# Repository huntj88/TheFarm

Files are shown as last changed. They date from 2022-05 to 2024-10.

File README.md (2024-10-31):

# TheFarm
High Pressure Aeroponics Experiment - <a href="https://photos.app.goo.gl/xgiAT7T5yuNJSb9R8">Project photo/video album</a>

Lettuce
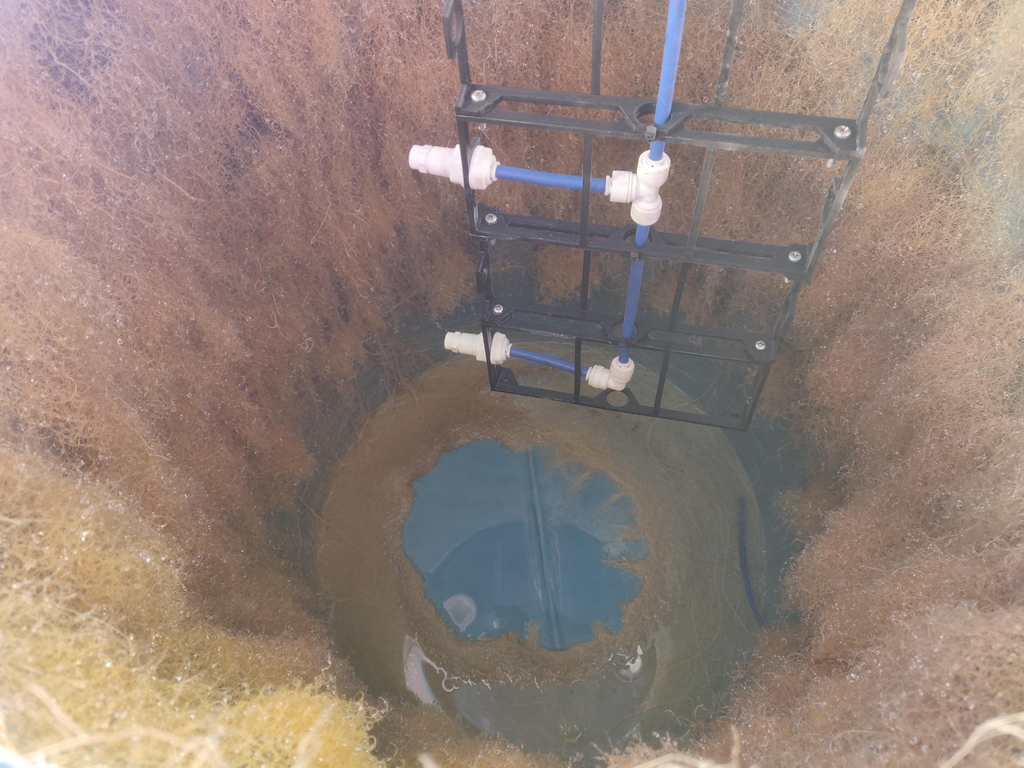
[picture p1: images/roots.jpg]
Lettuce


## Features
* High pressure dispersion system
  * Maximized water usage, minimized waste that is drained off
  * Rotary Dispersion system
    * Equal dispersion
    * High plant/nozzle ratio
    * Very few nozzles to maintain pressure through the system
      * This could be achieved by different watering zones that turn on sequentially to maintain pressure, but some water is wasted at the start/end when pressure is not enough for aerosolization to occur.
* Automatic LED Lighting Configurable by software.
* Environmental Monitoring / Correction
  * Temperature and Humidity Monitoring
  * Automatic humidity correction
    * humidifier enabled based on vapor pressure deficit
    * Doing this in a grow tent was crucial for maintaining correct humidity
  * No Temperature Control, at the mercy of my decently insulated garage.
* Time Lapse Camera
  * Old Android device with an app that took a picture and uploaded it to S3. App was triggered periodically over ADB from a raspberry pi.
* Water reservoir level monitoring
  * Sonic sensor was used to find depth of the water tank, which was converted into a percent of remaining water.
* The Software integrated all of the above together
  * Based on events, the whole system is reactive to new data.
  * Historical events are Recorded in InfluxDB time series database.
  * Devices are controlled in a variety of manners
    * Wifi using mqtt
    * USB (android camera only)
    * Smart power strips with local network api.
      * Turning on on the High Pressure pump periodically.
      * Controlling lights on/off cycles
  * Energy Monitoring with smart power strips.

## Reliability
High reliability was a priority. This is the only project I've had where I was really forced to wait around on the time scale that plants grow at. This is magnified by the use of aeroponics which allows the roots to dry out very quickly if something goes wrong. Starting over is no fun.

There was at least two times where I left home for awhile, only to come back to my plants being dead. There were several other occasions where my plants were effecively on manual life support while I debugged issues.

I spent a lot of time ensuring my plants wouldn't die on me, and that everything would come back online automatically after events like a power outage, network issues, process failures, etc.

For my most recent crop, I let it do it's thing for weeks at a time without any intervention except to refill consumables.

## Barrel Changes

### V1
Initially I used pvc to make net cup mounts because it was readily available. Unfortunately cuttings ovals into the barrel was pretty time consuming. I also should've cut the pvc closer to the barrel, as it prevented water from getting to the base of the roots.

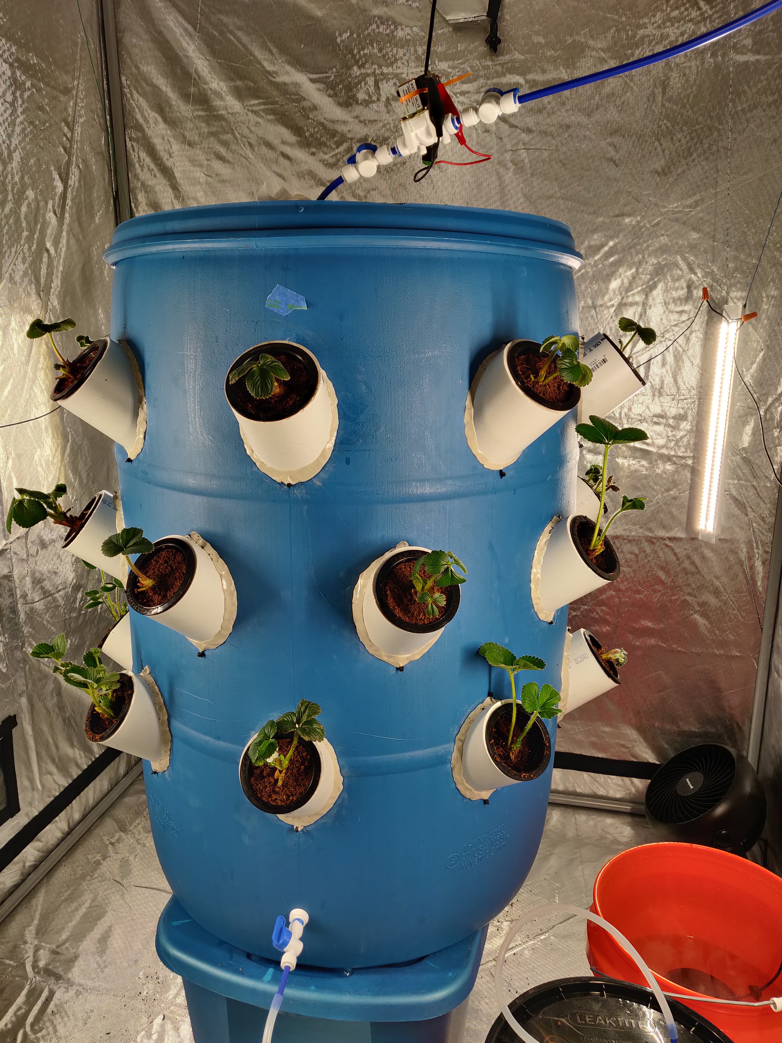
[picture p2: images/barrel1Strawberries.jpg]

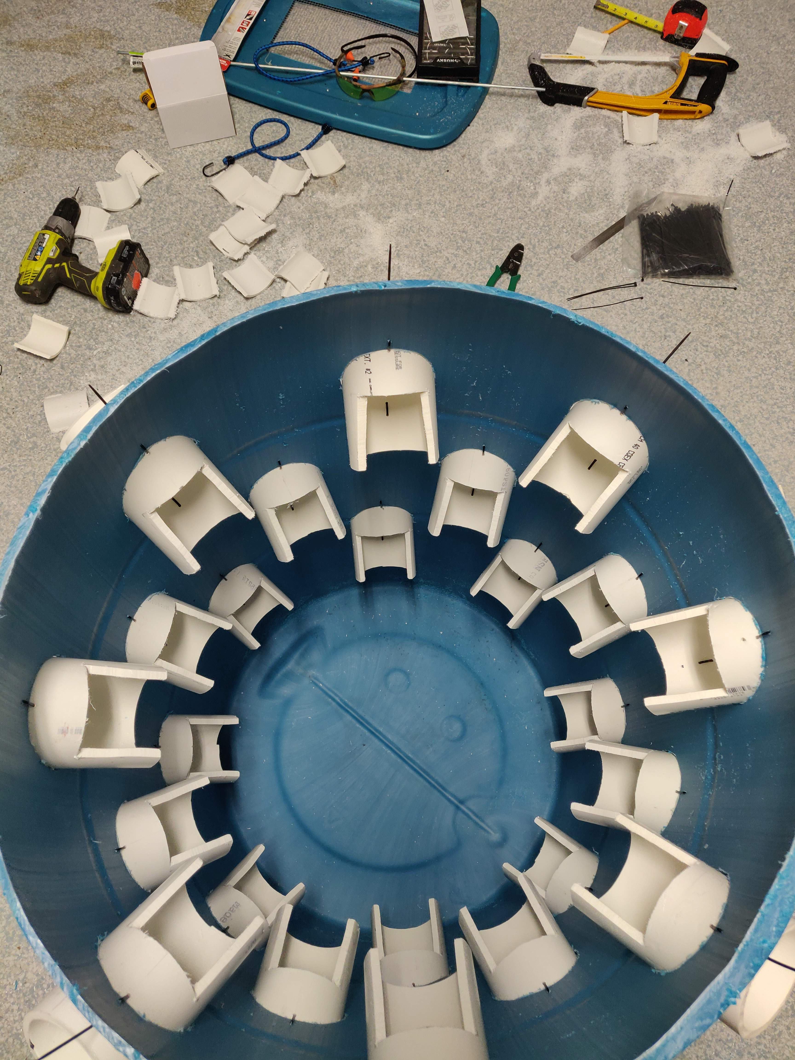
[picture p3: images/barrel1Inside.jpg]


This setup did work for strawberries until I killed my plants from a software issue, but I started with dormant bare root strawberry plants that had roots long enough to not cause issues.

I tried on lettuce and this setup did not work at all.

---

### V2
For V2 of the barrel I wanted to cut down on manual labor for myself, so I designed this net cup bracket and 3D printed 48 of them. I used a 3 inch hole saw to cut the holes, and secured the brackets in place with stainless steel machine screws.

The curvature is TINY bit too aggressive, so I would fix that If I printed a new batch.

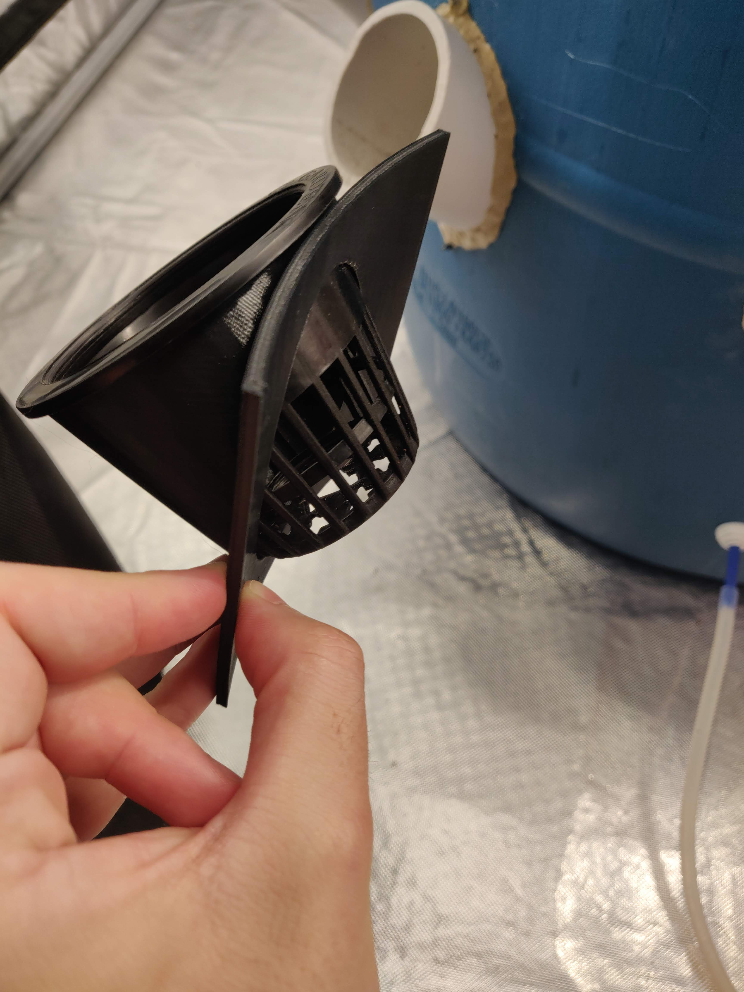
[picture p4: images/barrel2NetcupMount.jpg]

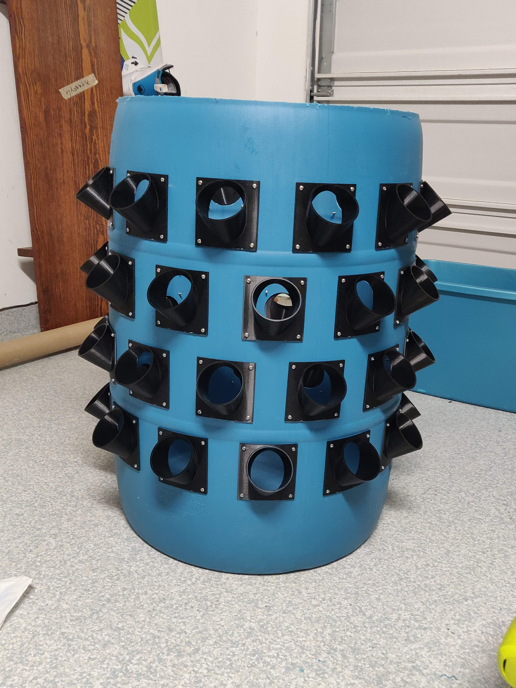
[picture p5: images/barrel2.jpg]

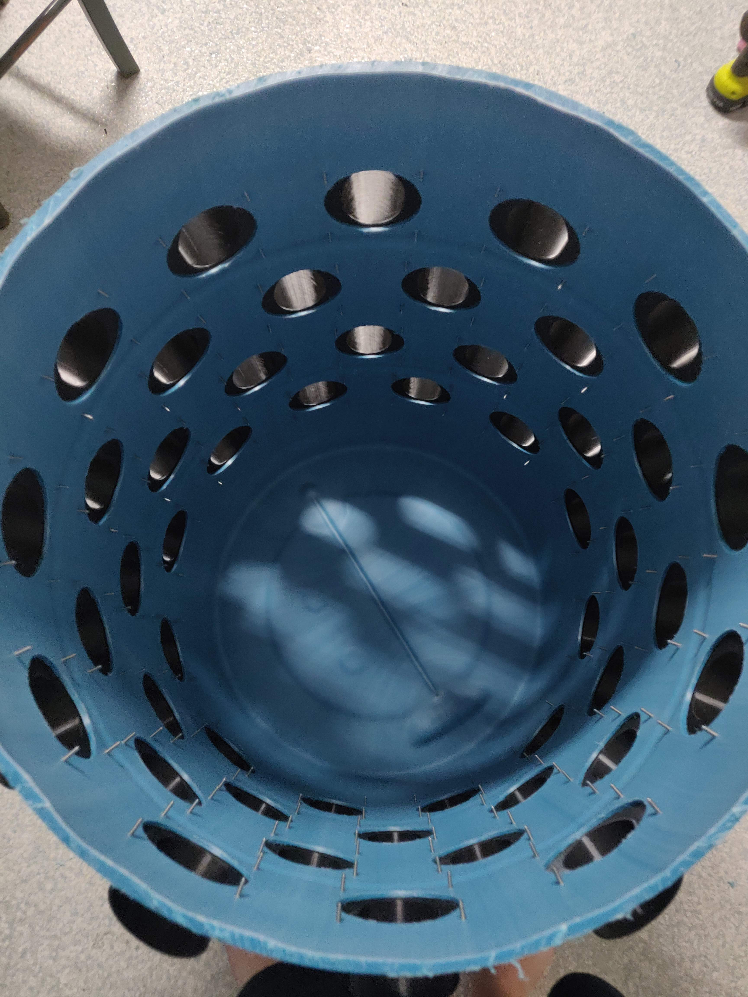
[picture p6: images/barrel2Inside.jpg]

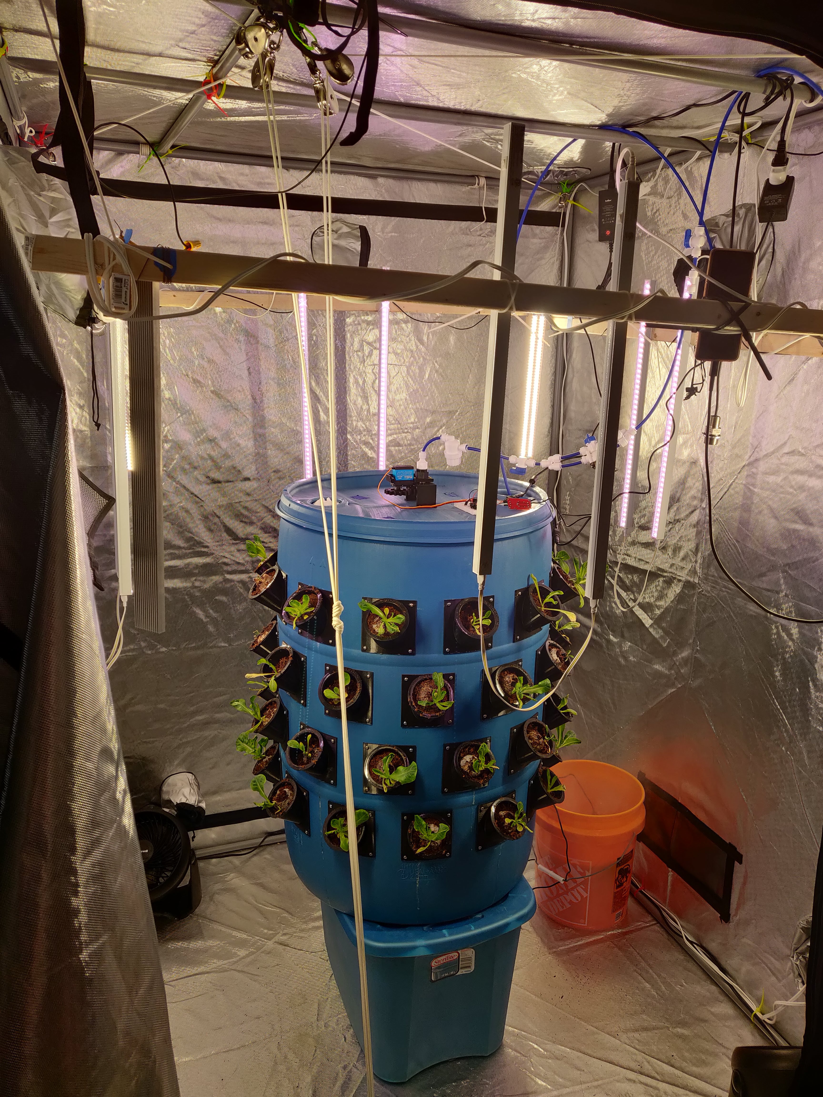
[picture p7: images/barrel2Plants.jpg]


## Mister changes
I started out with Knex just to understand the spray pattern my misters had

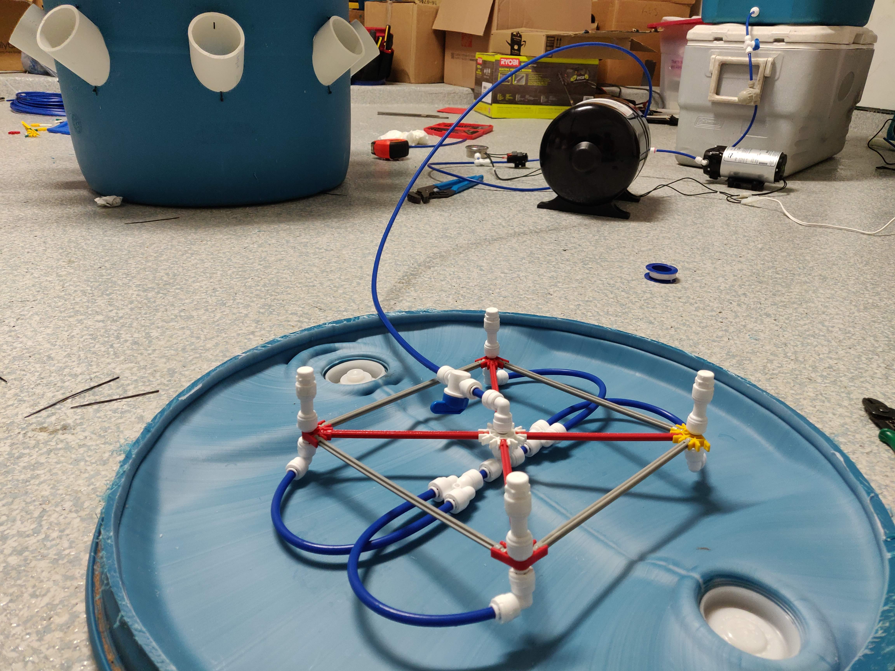
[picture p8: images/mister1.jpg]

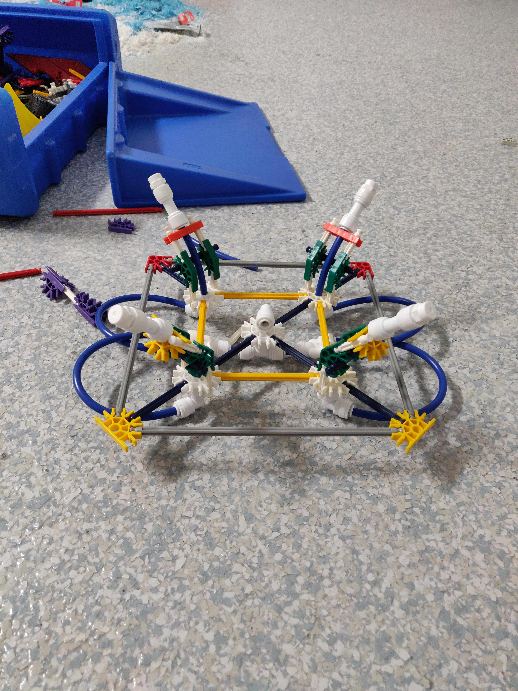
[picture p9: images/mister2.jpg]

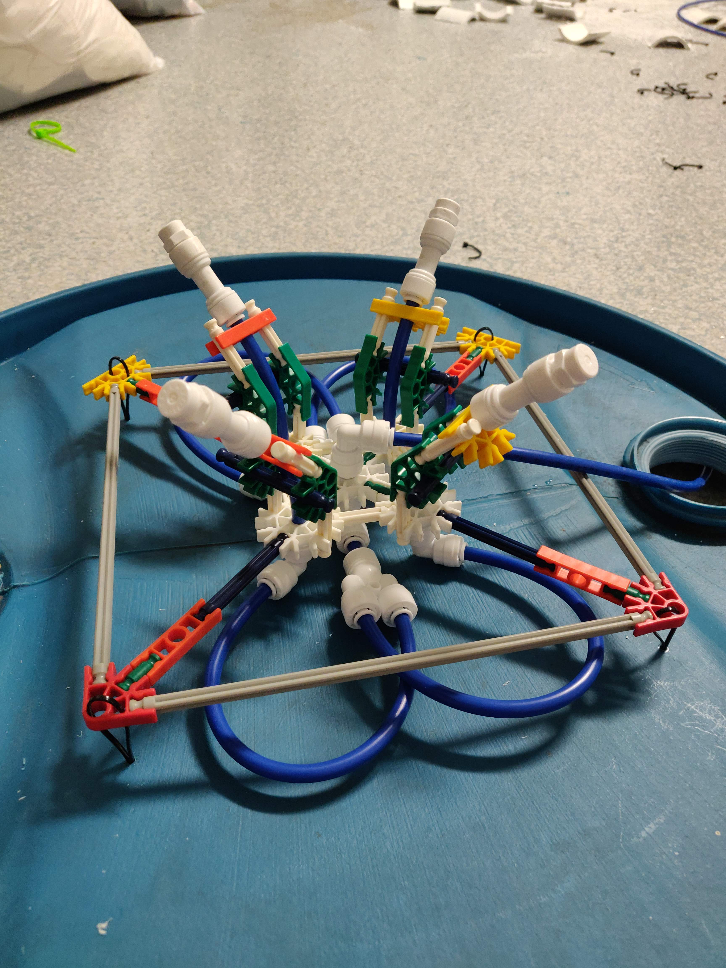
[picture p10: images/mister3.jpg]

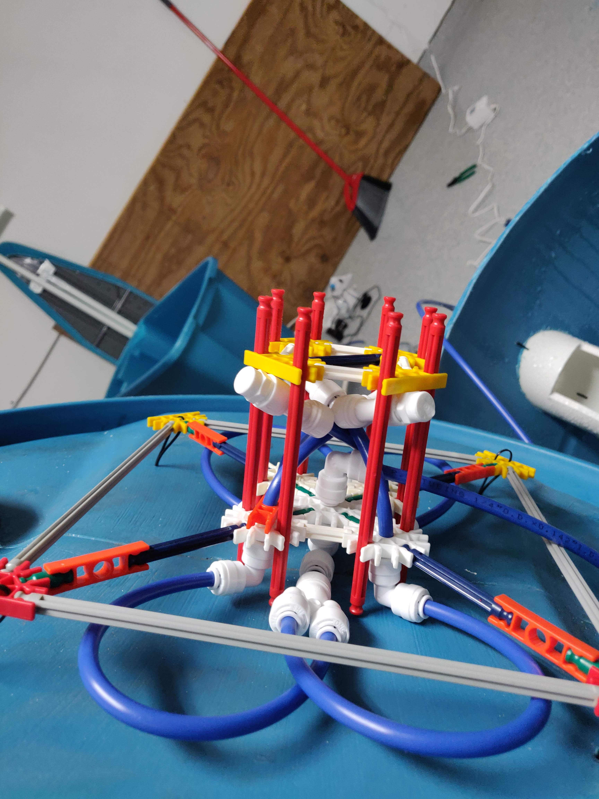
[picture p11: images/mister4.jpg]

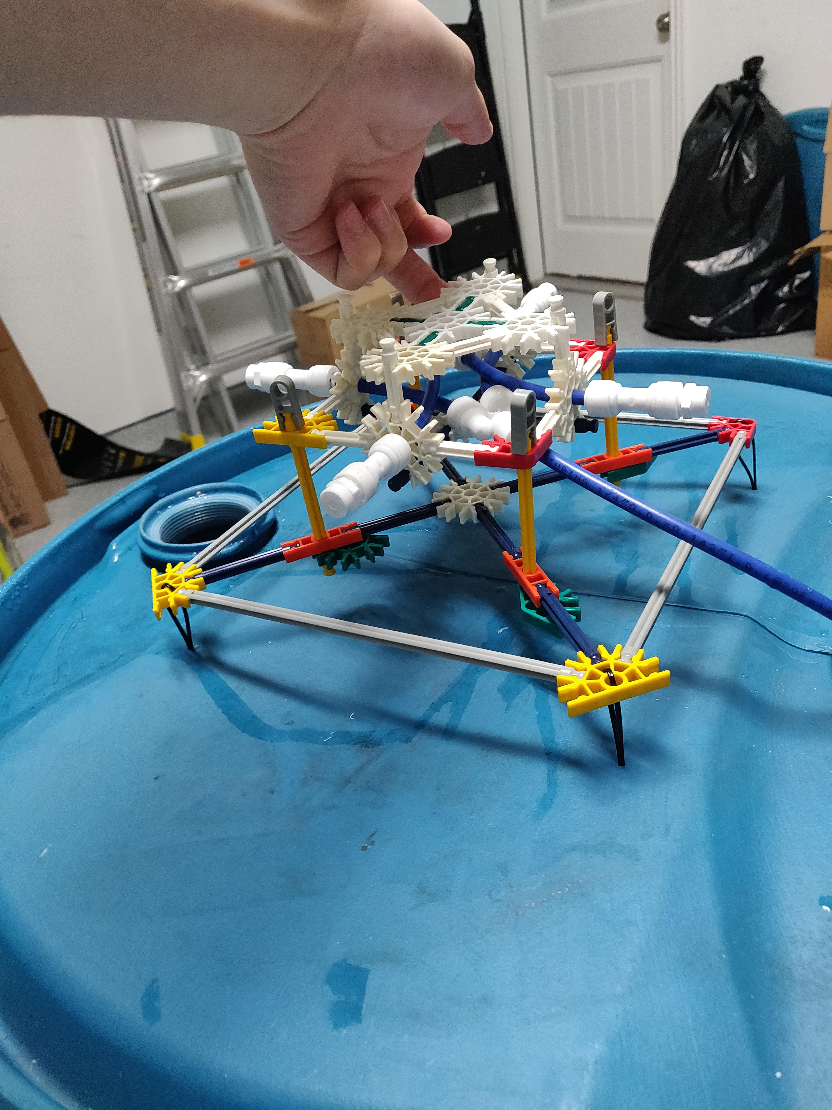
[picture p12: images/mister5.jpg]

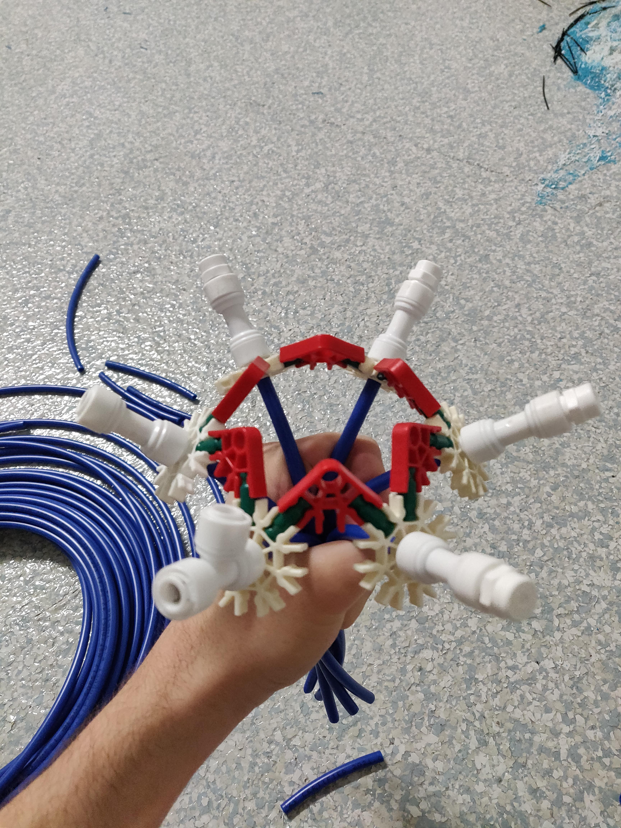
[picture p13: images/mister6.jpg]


The below mister is the first one I actually tried to grow plants with, although I quickly moved on.

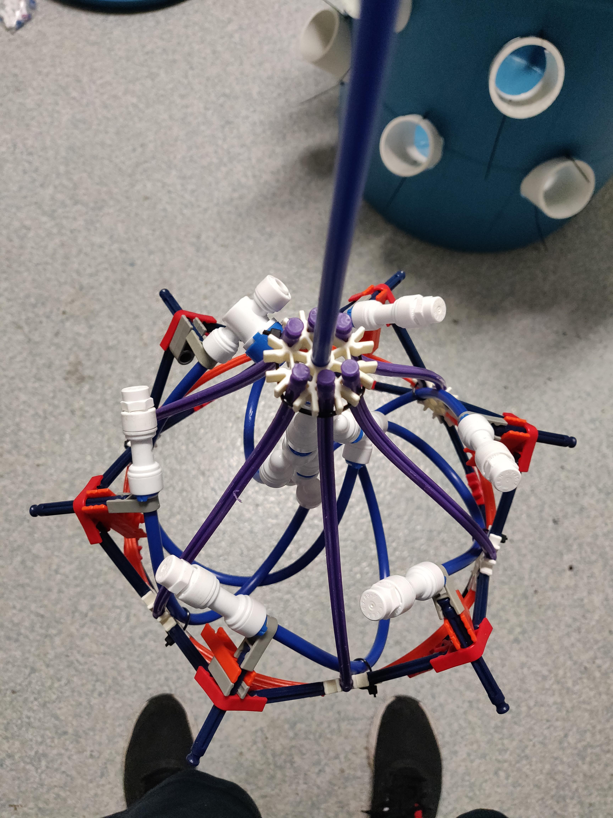
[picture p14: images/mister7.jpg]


---

This one could separately control the water flow in the top and bottom. Was not super great, but an improvement over the Knex designs

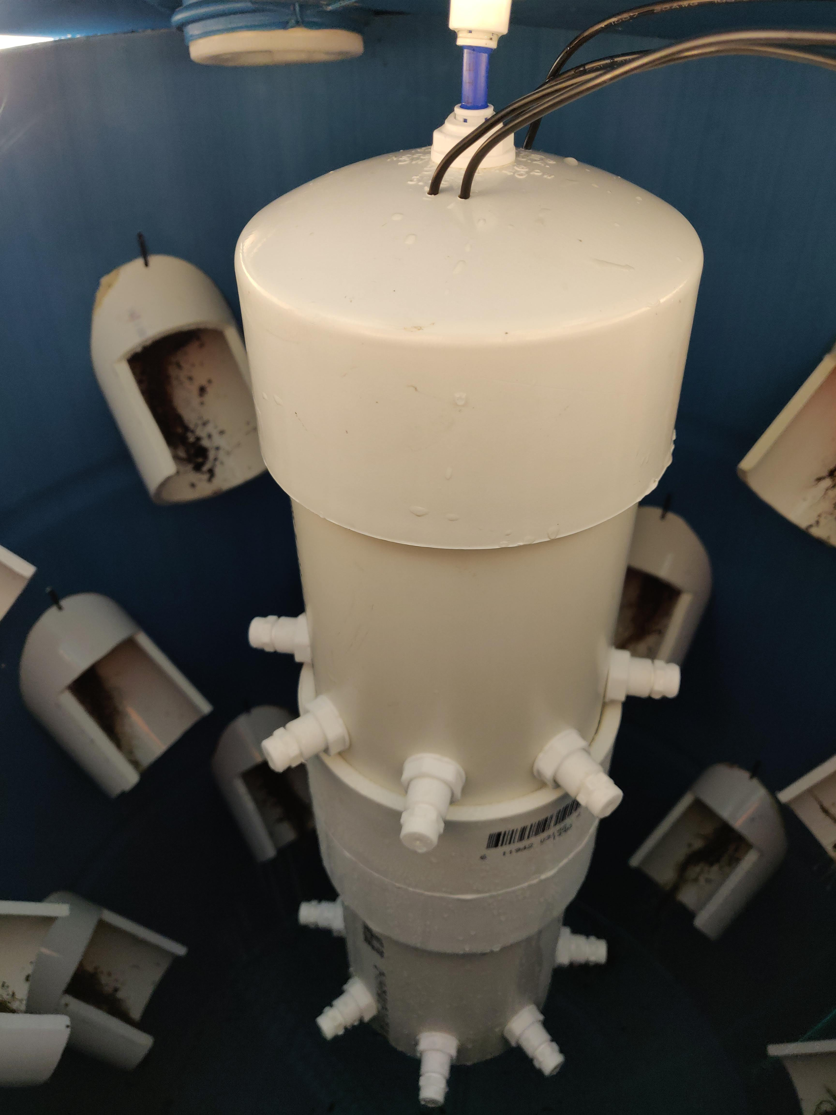
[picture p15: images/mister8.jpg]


---

This next was modular and could stack vertically. I was able to play with the vertical spacing to distribute water where I wanted it. 

Although an improvement, it had a major problem of a long pressurization period due to having so many nozzles. Lots of wasted water that wasn't aerosolized.

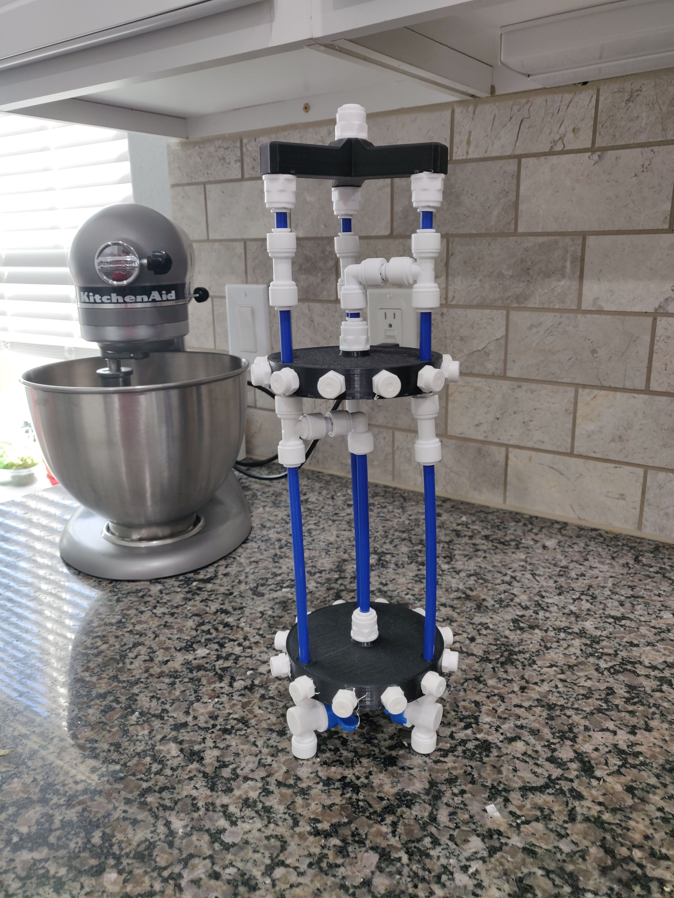
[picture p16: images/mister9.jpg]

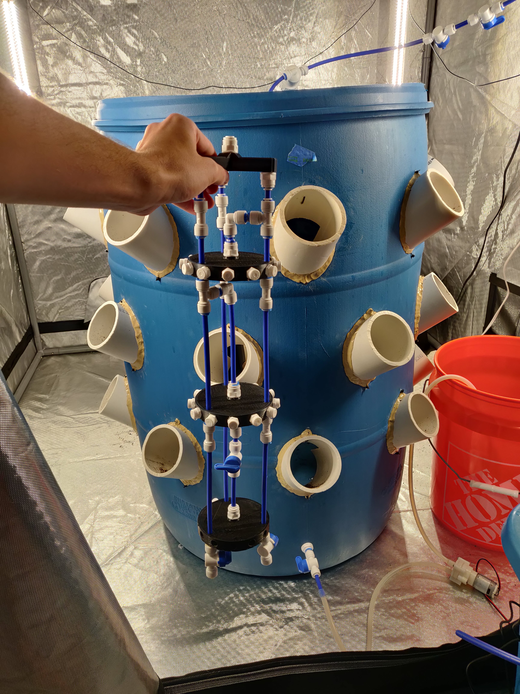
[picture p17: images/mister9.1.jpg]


---

Rotary Dispersion system - This one ended up working really well

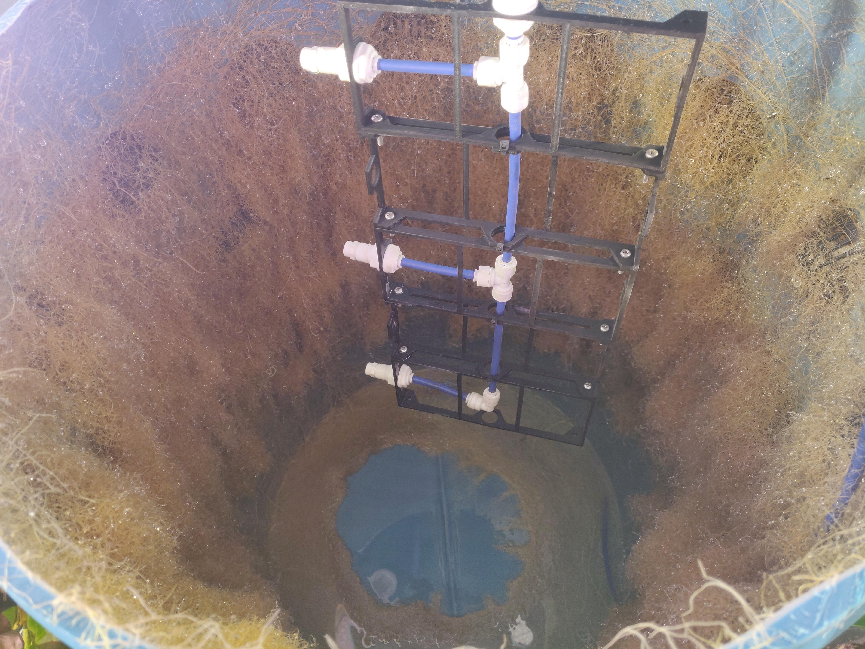
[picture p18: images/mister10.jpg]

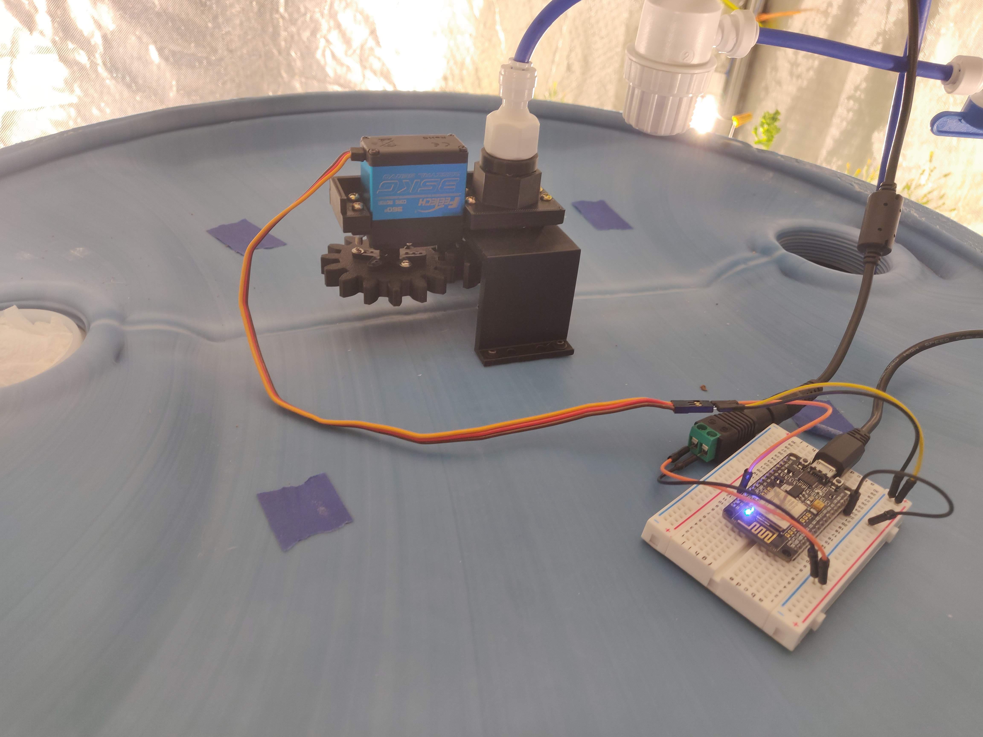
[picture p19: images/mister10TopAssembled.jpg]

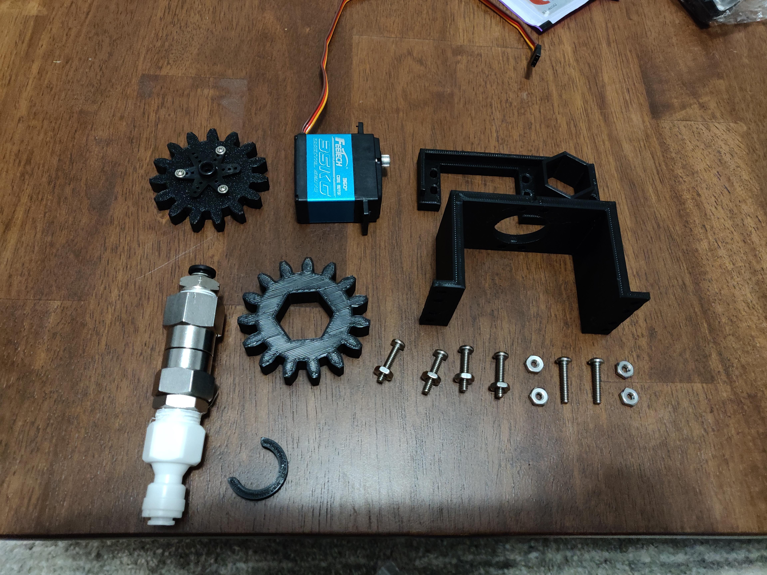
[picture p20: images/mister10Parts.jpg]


<a href="https://photos.google.com/share/AF1QipN4WQcN4S6AX1Nvl3MuYThQZdT2KUuTPvhOaKNPEQhu93empHC7coNHhumvaoyn5g/photo/AF1QipPuxE0sy1xfddFc1j102-yCW6brzKu2pu6SkxFH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">Video of it in action</a>

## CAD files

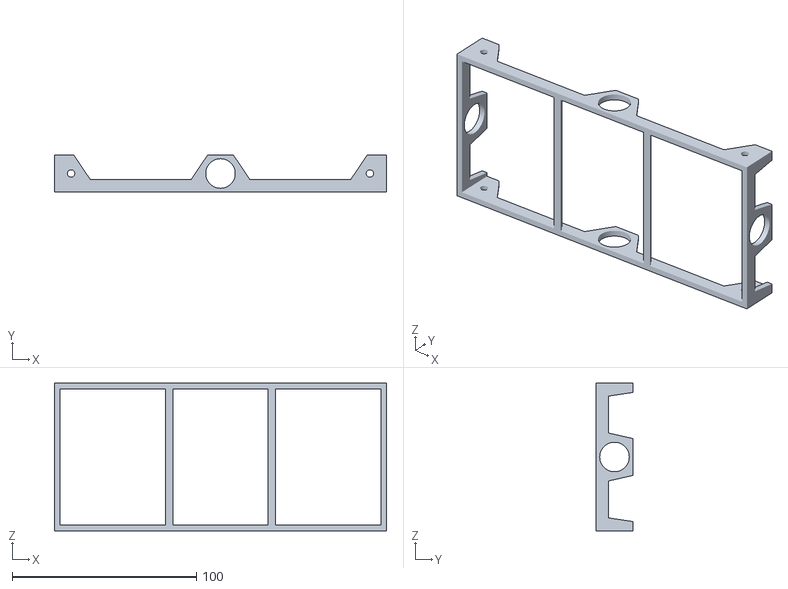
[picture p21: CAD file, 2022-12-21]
cad/rotationIrrigation/support.stl
180.0 x 20.0 x 80.0

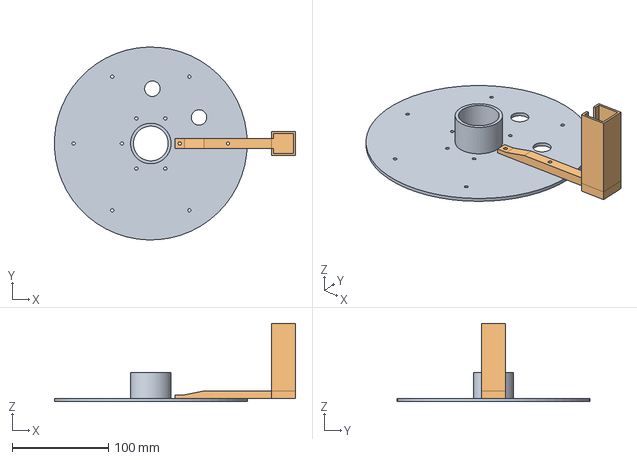
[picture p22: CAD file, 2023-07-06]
cad/segments.FCStd
249.8 x 199.9 x 81.0 mm

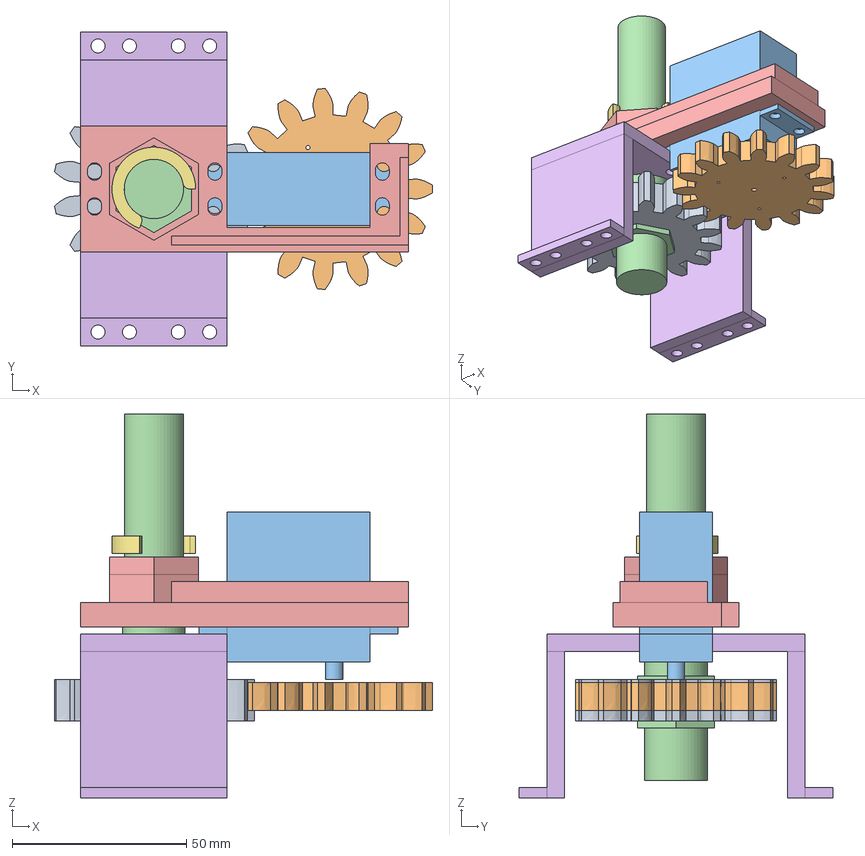
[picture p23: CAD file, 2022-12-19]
cad/rotationIrrigation/rotationIrrigation.FCStd
108.4 x 90.0 x 110.0 mm

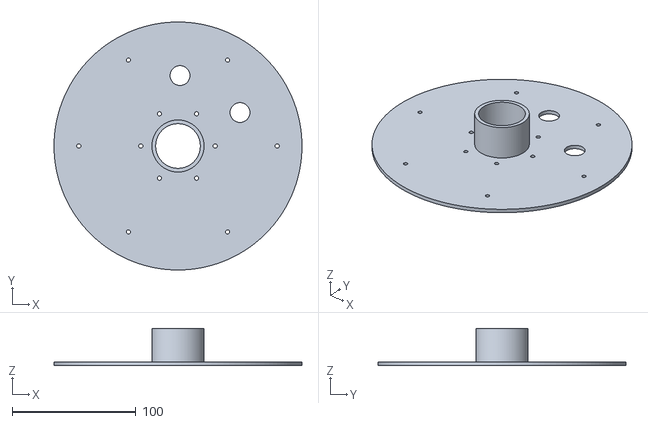
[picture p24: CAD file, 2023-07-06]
cad/segments-holder-bottom.stl
200.0 x 199.9 x 30.0

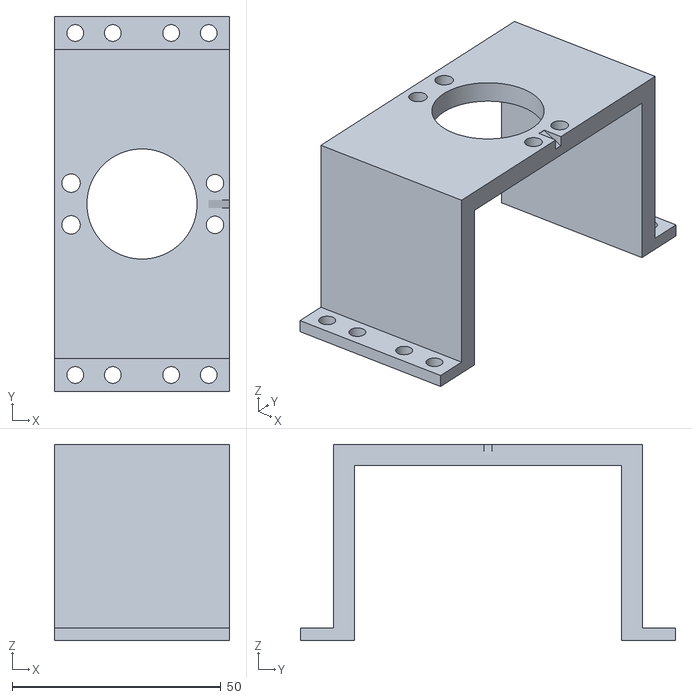
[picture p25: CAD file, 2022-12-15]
cad/rotationIrrigation/legs.stl
42.0 x 90.0 x 47.0

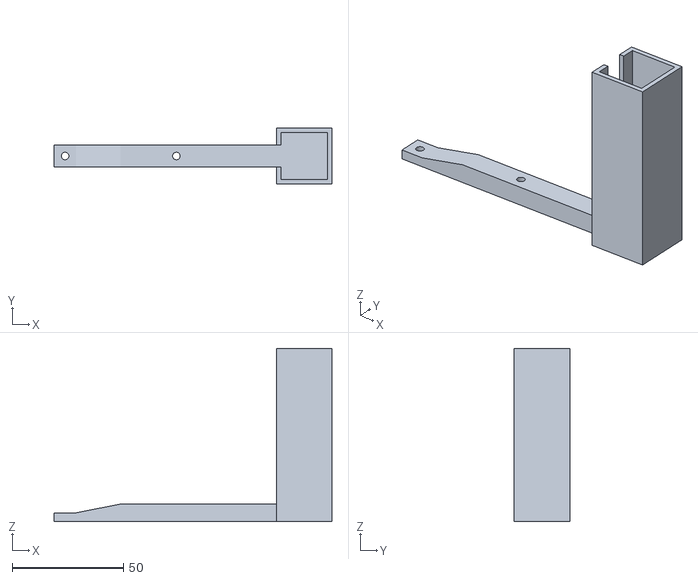
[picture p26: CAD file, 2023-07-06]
cad/segments-BaseLight.stl
125.0 x 25.0 x 78.0

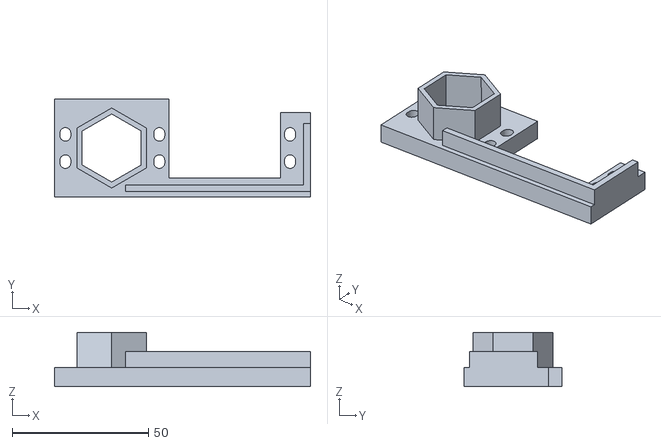
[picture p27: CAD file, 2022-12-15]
cad/rotationIrrigation/frame.stl
94.0 x 36.0 x 20.0

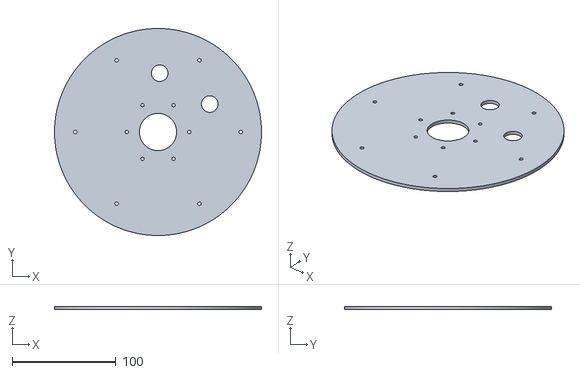
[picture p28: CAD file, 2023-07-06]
cad/segments-holder-top.stl
200.0 x 199.9 x 3.00

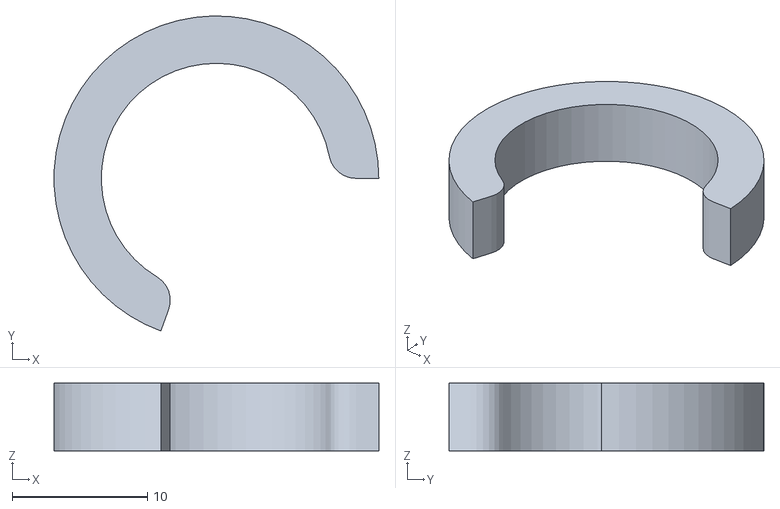
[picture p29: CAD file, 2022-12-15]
cad/rotationIrrigation/clip.stl
24.0 x 23.3 x 5.00

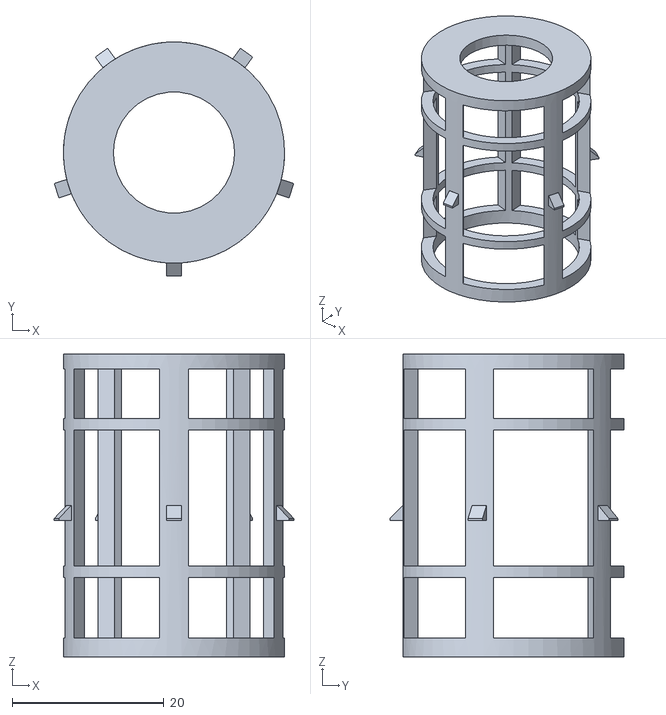
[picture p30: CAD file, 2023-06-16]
cad/segment-mister.stl
31.6 x 30.9 x 40.0

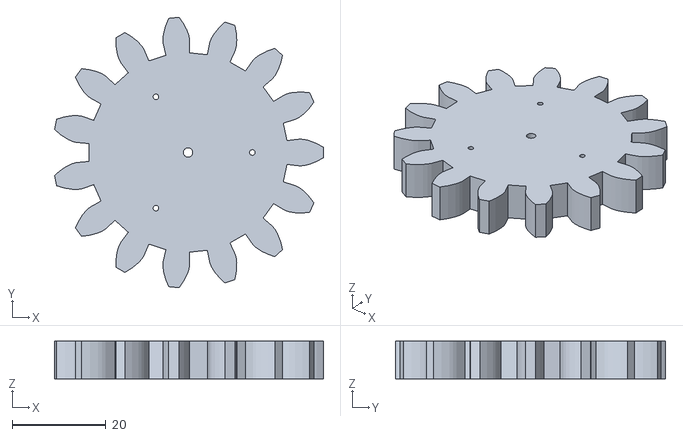
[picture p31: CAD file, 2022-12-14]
cad/rotationIrrigation/gear2.stl
57.4 x 57.7 x 8.00

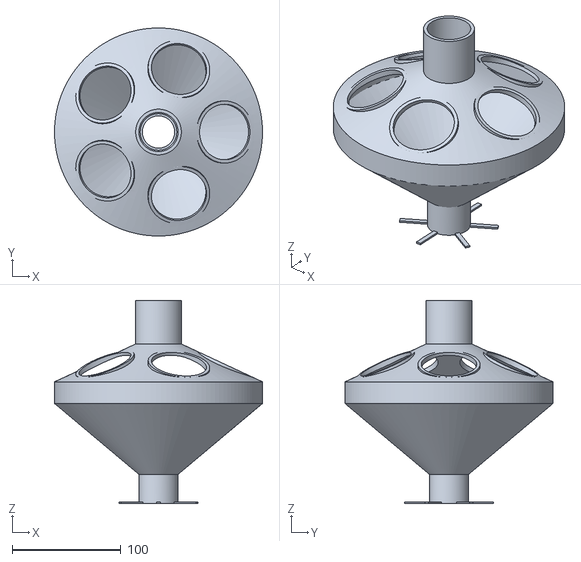
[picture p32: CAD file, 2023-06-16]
cad/segment.stl
191.1 x 191.0 x 186.7

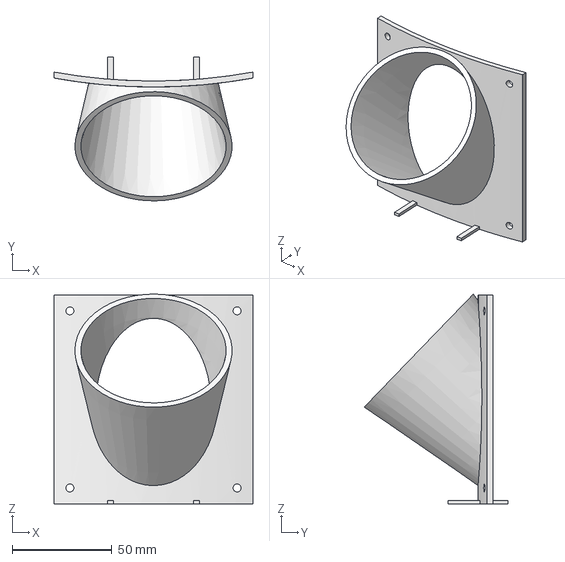
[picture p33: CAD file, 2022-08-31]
cad/bracket3Inch.FCStd
100.0 x 72.2 x 105.4 mm

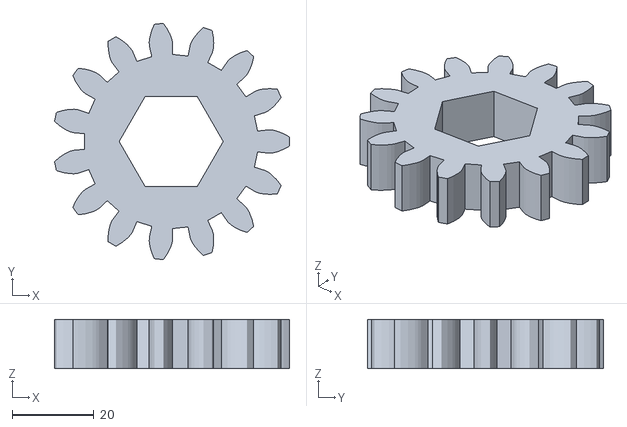
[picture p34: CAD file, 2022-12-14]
cad/rotationIrrigation/gear1.stl
57.4 x 57.7 x 12.0

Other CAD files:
cad/irrigation-splitter.stl
cad/irrigation-mister.stl
cad/irrigation.FCStd
cad/bracket3Inch.stl

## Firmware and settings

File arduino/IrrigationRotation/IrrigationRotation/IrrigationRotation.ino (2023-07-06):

#include <Servo.h>

Servo servo;
int minPulseWidth = 500;
int maxPulseWidth = 2500;
int pulseWidthDiff = maxPulseWidth - minPulseWidth;
int numSecondsToWater = 6;
int delayMilliPerDegreeWater = numSecondsToWater * 1000 / 360.0;

int numSecondsToReturn = 6;
int waterPin = 0; // D3

void setup() {
  // setup and turn on water
  pinMode(waterPin, OUTPUT);
  servo.attach(2, minPulseWidth, maxPulseWidth); // D4
}

void loop() {
  waterAndRotateCounterClockwise();

  delay(1000);

  resetRotation();
  
  // pause until power cuts out
  delay(1000 * 60 * 60);
}

void waterAndRotateCounterClockwise() {
  digitalWrite(waterPin, HIGH);
  
  int degreeToIncrement = 2;

  // SLOW START ROTATION START
  for (float angle = 0; angle < 8; angle += degreeToIncrement) {
    servo.writeMicroseconds((angle / 360.0 * pulseWidthDiff) + minPulseWidth);
    delay(delayMilliPerDegreeWater * degreeToIncrement * 4);
  }

  for (float angle = 8; angle < 16; angle += degreeToIncrement) {
    servo.writeMicroseconds((angle / 360.0 * pulseWidthDiff) + minPulseWidth);
    delay(delayMilliPerDegreeWater * degreeToIncrement * 3);
  }

  for (float angle = 16; angle < 24; angle += degreeToIncrement) {
    servo.writeMicroseconds((angle / 360.0 * pulseWidthDiff) + minPulseWidth);
    delay(delayMilliPerDegreeWater * degreeToIncrement * 2);
  }
  // SLOW START ROTATION END

  // angle starts from end of slow rotation
  for (float angle = 24; angle < 360; angle += degreeToIncrement) {
    servo.writeMicroseconds((angle / 360.0 * pulseWidthDiff) + minPulseWidth);
    turnOffWaterIfEnding(angle);
    delay(delayMilliPerDegreeWater * degreeToIncrement);
  }
  
  servo.writeMicroseconds(maxPulseWidth);
}

void turnOffWaterIfEnding(int angle) {
  // turn water pressure off 1 second before end of irrigation period, remaining pressure in pipe is enough to finish
    int turnOffWaterDegrees = 360 - (1000 / delayMilliPerDegreeWater);
    if (angle >= turnOffWaterDegrees) {
      digitalWrite(0, LOW);
    }
}

void resetRotation() {
    int delayMilliPerDegreeReturn = numSecondsToReturn * 1000 / 360.0;
  for (float angle = 360; angle > 0; angle -= 1) {
    servo.writeMicroseconds((angle / 360.0 * pulseWidthDiff) + minPulseWidth);
    delay(delayMilliPerDegreeReturn);
  }

  servo.writeMicroseconds(minPulseWidth);
}

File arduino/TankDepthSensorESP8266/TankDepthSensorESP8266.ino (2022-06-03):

#include "secrets.h"
#include <ESP8266WiFi.h>
#include "Adafruit_MQTT.h"
#include "Adafruit_MQTT_Client.h"

//#define MQTT_SERVER      "192.168.1.196"
#define MQTT_SERVER      "192.168.1.83"
#define MQTT_SERVERPORT  1883                   // use 8883 for SSL

int trig = 4; // Attach Trig of ultrasonic sensor to pin D2
int echo = 5; // Attach Echo of ultrasonic sensor to pin D1

WiFiClient client;
Adafruit_MQTT_Client mqtt(&client, MQTT_SERVER, MQTT_SERVERPORT); // TODO: username and password
Adafruit_MQTT_Publish publishTopic = Adafruit_MQTT_Publish(&mqtt, "humidifierTankDepthSensor");

void setup() {
  Serial.begin(9600);

  delay(1000);

  // Connect to WiFi access point.
  Serial.println(); Serial.println();
  Serial.print("Connecting to ");
  Serial.println(SECRET_SSID);

  WiFi.begin(SECRET_SSID, SECRET_PASS);
  while (WiFi.status() != WL_CONNECTED) {
    delay(2000);
    Serial.print(".");
  }
  Serial.println();

  Serial.println("WiFi connected");
  Serial.println("IP address: "); Serial.println(WiFi.localIP());
  WiFi.setAutoReconnect(true);
  WiFi.persistent(true);

}

void loop() { 
  MQTTConnect();
  float distanceCm = distanceCentimetersAvg();
  Serial.println(distanceCm);
  publishTopic.publish(distanceCm);
  delay(30000); // TODO: 2 minute delay
}

float distanceCentimetersAvg() {
  float sum = 0.0;
  for (int i = 0; i < 10; i++) {
    sum += distanceCentimeters();
    delay(100); 
  }
  return sum / 10.0;
}

float distanceCentimeters() {
  // The PING is triggered by a HIGH pulse of 2 or more microseconds.
  // Give a short LOW pulse beforehand to ensure a clean HIGH pulse:
  pinMode(trig, OUTPUT);
  digitalWrite(trig, LOW);
  delayMicroseconds(2);
  digitalWrite(trig, HIGH);
  delayMicroseconds(5);
  digitalWrite(trig, LOW);
  
  // echo pin is used to read the signal from the PING: a HIGH
  // pulse whose duration is the time (in microseconds) from the sending
  // of the ping to the reception of its echo off of an object.
  pinMode(echo, INPUT);
  long duration = pulseIn(echo, HIGH);
  return microsecondsToCentimeters(duration);
}

float microsecondsToCentimeters(long microseconds) {
  // The speed of sound is 340 m/s or 29 microseconds per centimeter.
  // The ping travels out and back, so to find the distance of the
  // object we take half of the distance travelled.
  return microseconds / 29.0 / 2.0;
}

// invoke in loop function
void MQTTConnect() {
  if (mqtt.connected()) {
    return;
  }

  Serial.print("Connecting to MQTT... ");
  // retry infinitely
  int8_t responseCode;
  while ((responseCode = mqtt.connect()) != 0) { // connect will return 0 for connected
       Serial.println(mqtt.connectErrorString(responseCode));
       Serial.println("Retrying MQTT connection in 30 seconds...");
       mqtt.disconnect();
       delay(30000);
  }
  Serial.println("MQTT Connected!");
}

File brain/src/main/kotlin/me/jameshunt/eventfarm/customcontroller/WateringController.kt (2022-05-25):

package me.jameshunt.eventfarm.customcontroller

import io.reactivex.rxjava3.core.Observable
import io.reactivex.rxjava3.disposables.Disposable
import me.jameshunt.eventfarm.core.*
import java.time.Instant
import java.time.temporal.ChronoUnit
import java.util.*

// TODO: handle restarts gracefully, check when last watered using values in a DB (input on event, or schedule time?)
/**
 * Controls how often plants are watered.
 * When the amount of water remaining in the reservoir gets low, conserve water mode is enabled.
 */
class WateringController(
    override val config: Config,
    private val scheduler: Scheduler,
    private val eventManager: IInputEventManager,
    private val logger: Logger,
) : Configurable, Scheduler.Schedulable {
    data class Config(
        override val id: UUID,
        override val className: String,
        val wateringOutputId: UUID,
        val wateringOutputIndex: Int?,
        val waterDepthInputId: UUID,
        val waterDepthIndex: Int?, // TODO: waterDepthInputIndex
        val periodMillis: Long,
        val durationMillis: Long,
        val conserveWaterUsagePercent: Float, // 0f-1f
        val conserveWaterReservoirPercent: Float, // 0f-1f
    ) : Configurable.Config

    override fun listenForSchedule(onSchedule: Observable<Scheduler.ScheduleItem>): Disposable {
        return onSchedule.switchMap {
            when {
                it.isStarting -> handle()
                it.isEnding -> Observable.empty()
                else -> Observable.error(IllegalStateException("Should not be possible"))
            }
        }.subscribe({}, { throw it })
    }

    private fun handle(): Observable<Long> {
        return eventManager
            .waitForValueOrDefaultThenInterval(
                periodMillis = config.periodMillis,
                inputId = config.waterDepthInputId,
                inputIndex = config.waterDepthIndex,
                default = TypedValue.Percent(1f) // TODO: use latest value from db before restart
            )
            .map { percent -> getWateringDurationMillis(percent) }
            .doOnNext { durationMillis ->
                val now = Instant.now()
                val end = now.plusMillis(durationMillis)
                scheduler.schedule(
                    Scheduler.ScheduleItem(
                        config.wateringOutputId,
                        config.wateringOutputIndex,
                        TypedValue.Bool(true),
                        now,
                        end
                    )
                )
            }
    }

    private fun getWateringDurationMillis(reservoirPercentEvent: Input.InputEvent): Long {
        // only use reservoir percent if there is a recent value
        if (reservoirPercentEvent.time.isBefore(Instant.now().minus(6, ChronoUnit.HOURS))) {
            logger.warn("Reservoir depth value too old for conserve water check, using default behavior", null)
            // disregard depth and use normal duration
            return config.durationMillis
        }

        val reservoirPercent = (reservoirPercentEvent.value as TypedValue.Percent).value

        val conserveWaterReservoirPercent = config.conserveWaterReservoirPercent.withPercentValidation()
        val conserveWaterUsagePercent = config.conserveWaterUsagePercent.withPercentValidation()
        return if (reservoirPercent < conserveWaterReservoirPercent) {
            val formattedPercent = "${reservoirPercent * 100f}".takeLast(5)
            logger.warn("Reservoir depth at $formattedPercent, Conserving water", null)
            // if: conserveWaterReservoirPercent = 0.15
            // if: conserveWaterUsagePercent = 0.6
            // then: when less than 15% remaining in tank only use 60% watering duration
            (config.durationMillis * conserveWaterUsagePercent).toLong()
        } else {
            config.durationMillis
        }
    }

    private fun Float.withPercentValidation(): Float {
        return this.also { TypedValue.Percent(it) }
    }
}

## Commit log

2021-12-20 added android remote camera app
2021-12-21 cleanup, added sqlite, and power management/logging barebones
2021-12-21 getting ready for smart power strip
2021-12-27 better logging, migrate from timer to ScheduledThreadPoolExecutor, retry for LightScheduler
2022-03-27 how a PID controller might be structured, and cleanup
2022-03-27 first working prototype of event based architecture
2022-03-29 TypedValue categories of units that measure the same thing, for easy conversions, played around with new approach to a device
2022-05-04 Integrated sonar tank depth sensor
2022-05-05 convert depth sensor to be a return cm as a float
2022-05-05 removed input specific hs300 lib from main DI graph, basic retries of depth sensor IO, cleanup
2022-05-10 esp8266 depth sensor publishes mqtt values
2022-05-10 wifi mqtt depth sensor cleanup
2022-05-14 integrating ezo hum sensor using esp8266 and mqtt
2022-05-14 vpd calculation works, vpd controller controls humidity properly, deprecated old depth sensor
2022-05-14 Made pressure pump controller. runs on a timer, and will not pump when reservoir is below 2 percent
2022-05-14 made the vpd controller more restart tolerant. rebooting with the humidifier in the on state made it stay on forever. I made a cloud inside my strawberry tent 😆
2022-05-14 remote camera improvements
2022-05-15 deployment code and remote camera basic integration
2022-05-15 mqtt sensors connect to raspberry pi now
2022-05-15 used PeriodicController for drain pump and time-lapse camera
2022-05-15 added exhaust fan periodic controller
2022-05-25 reconnect esp8266 wifi test, copy takePicture, logging, fixed concurrent modification exception, todos
    [EzoHumHumidityTempSensor.ino, WateringController.kt]
2022-06-04 start adb on camera input started, close publish subjects, improved install script
2022-06-04 filter out old values from vpd calculation
2022-06-25 Added irrigation cad file
    [irrigation.FCStd]
2022-06-26 mister adjustments and added top splitter
    [irrigation-mister.stl, irrigation-splitter.stl, irrigation.FCStd]
2022-06-26 corrected measurements on cad models
    [irrigation-mister.stl, irrigation-splitter.stl, irrigation.FCStd]
2022-06-27 Fixed cad measurements
    [irrigation-mister.stl, irrigation-splitter.stl, irrigation.FCStd]
2022-06-29 Fixed measurements, added removable tabs to anchor mister to 3d printer surface (should be used with a brim)
    [irrigation-mister.stl, irrigation-splitter.stl, irrigation.FCStd]
2022-07-06 made horizontal 1/8 npt holes slightly bigger, added surface adhesion tabs to splitter
    [irrigation-mister.stl, irrigation-splitter.stl, irrigation.FCStd]
2022-07-09 Found measurements that aren't too tight for the threaded parts
    [irrigation-mister.stl, irrigation-splitter.stl, irrigation.FCStd]
2022-07-25 3d model for barrel bracket
    [bracket.FCStd]
2022-07-26 cad model for 3 inch net cup bracket
    [bracket2.FCStd]
2022-07-29 Fixed bracket curvature, made netcup height 2mm taller, added bolt holes
    [bracket2.FCStd]
2022-07-29 Rotated model 180 degrees so the overhang faces the front. My printer has a fan blowing on the front
    [bracket.FCStd, bracket2.FCStd, bracket3Inch.FCStd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]
2022-07-31 Made bracket slightly more curved
    [bracket3Inch.FCStd, bracket3Inch.stl]
2022-08-31 Bracket changes
    [bracket3Inch.FCStd, bracket3Inch.stl]
2022-09-16 Added second hs300, install git automatically, temporarily disable, disabled exhaust fan and depth sensor for now
2022-11-15 Reset docker script Ran into a case where 'systemctl start docker' would fail after a power outage. Deleting all containers, images, network, volumes, runtimes, tmp, etc fixes the issue, but needs to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
2022-11-17 made pump rump after 200 minutes instead of 240, checked in rotation irrigation cad files
    [support-nexus.stl, support.FCStd]
2022-12-13 getting closer on measurements
    [support.FCStd]
2022-12-14 adding stlsof gears
    [support-gear1.stl, support-gear2.stl, support-nexus.stl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]
2022-12-14 new frame version
    [support.FCStd]
2022-12-14 modular legs idea, not finished
    [support.FCStd]
2022-12-14 bolt holes in legs
    [support.FCStd]
2022-12-15 better measurements, cleanup, added clip
    [support.FCStd]
2022-12-15 added stl files
    [support-clip.stl, support-frame.stl, support-legs.stl]
2022-12-19 improved mister support
    [support.FCStd, support.stl]
2022-12-19 cleanup files and naming for irrigation rotation cad
    [clip.stl, frame.stl, gear1.stl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]
2022-12-21 rotate servo for irrigation
2022-12-28 added relay to code
2023-02-21 added camera back
2023-06-01 segment design
    [segments.FCStd]
2023-06-03 Made segment mister shorter
    [segments.FCStd]
2023-06-03 made mister extend lower into bottom of segment
    [segment-mister.stl, segments.FCStd]
2023-06-16 adjusted spacing on mister, added stls
    [segment-mister.stl, segment.stl, segments.FCStd]
2023-07-06 segment holder and light attachment
    [segments-BaseLight.stl, segments-holder-bottom.stl, segments-holder-top.stl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]
